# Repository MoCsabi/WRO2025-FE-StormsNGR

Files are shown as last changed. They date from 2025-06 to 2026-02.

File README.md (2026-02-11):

# Introduction
We are the StormsNGR team from Hungary, and we competed in the 2025 WRO Future Engineers category. This was our second year competing after a very successful first year, for which you can find our documentation [here](https://github.com/MoCsabi/WRO2024-FE-StormsNGR). We will be keeping that repository as it is, and will be updating this repository for the 2025 season.

# Results
We once again managed to earn a spot on the podium with 3rd place, a result we are very proud of 😊. We will be keeping this repository as is to help those who are interested study our complete 2025 season solution. For the 2026 season you can follow our progress in the [WRO2026-FE-StormsNGR](https://github.com/MoCsabi/WRO2026-FE-StormsNGR) repository.

## The team
>Team members
- **Csaba Molnár** from [Budapest University of Technology and Economics](https://www.bme.hu/en) Faculty of Electrical Engineering and Informatics
  - csabi@molnarnet.hu
- **András Gräff** from [Budapest University of Technology and Economics](https://www.bme.hu/en) Faculty of Mechanical Engineering
  - andrasgraff@gmail.com
- **Levente Molnár** from [Sóskút Károly Andreetti elementary school](https://iskola.soskut.hu/)
  - levente@molnarnet.hu
>Coach
- József Balázs Gräff
  - graffjozsefb@gmail.com

Links to our socials:

- **Facebook**: https://www.facebook.com/stormsteam/
  - Here you can find updates about the team
- **YouTube**: https://www.youtube.com/channel/UCyzm_Su7qoRCof-ZpbG_9Ig
  - Here you can watch videos about past competitions
- **Instagram**: https://www.instagram.com/storms_team_hun/
  - Cool posts and updates about our, and our sister-team StormsRMS' preparation for upcoming competitions

# Abstract
Our solution is an autonomous car powered by a Raspberry Pi coded in Python, responsible for the main challenge logic, and an ESP microcontroller coded in C, responsible for controlling the motors and processing sensor data. The two devices communicate using UART. We use a 360° 2D LiDAR combined with a gyro to always know where the robot is on the mat. Detection of the traffic sign's color is done by combining the output of the LiDAR with the camera feed to know exactly where the object is. We use ackermann steering geometry calibrated so the car can leave the parking space in one continuous arc. Driving is powered by 1 DC motor through a differential gearbox designed from scratch, with a top speed of around 2.6 m/s.

# Table of contents

### [Our journey](/Our%20Journey.md)
### [Ideas and principles](/Ideas_and_principles.md)
### [Hardware documentation](/schemes/README.md)
### [Software documentation](/src/README.md)
### [measurement- The robot's mechanical characteristics](/The%20robot's%20mechanical%20characteristics.md)
### [RpiCode development tool documentation](/other/README.md)
### [Videos](/video/video.md)
### [Team Photos](/t-photos/)
### [Vehicle Photos](/v-photos/)

# Special thanks
Special thanks to Zsolt Molnár for all the mentoring he's done for us, József Molnár from the [Budapest University of Technology and Economics](https://www.bme.hu/) Faculty of Mechanical Engineering for helping us with the preparations, György Fenyvesi for helping us develop our prototype [custom made interconnect panel](/schemes/README.md/#custom-made-interconnect-panel-wiring-with-connections-labeled), and a bunch of others for helping us by reviewing all the documentation. And of course, to both our families for tolerating us taking up the entire living room with the robot mat 🙂.

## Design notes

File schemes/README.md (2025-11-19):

# Hardware documentation and setup guide
The robot is made up of a lot of different sensors, motors and two processing units, the ESP microcontroller and a Raspberry Pi. The car uses ackermann steering geometry and one DC motor through a motor controller with a differential gearbox we designed and printed from scratch. We had to create a lot of custom 3D printed components and even a custom interconnect panel to help with complicated wiring. The power to the robot is supplied by a 11.1V lithium battery and is later converted to 5V by a step-down module.

## List of components
We installed a lot of sensors and other components on the car, here is a list of each of them with a link and some additional notes:
- **Ackermann steering mechanism** and **base plates** [Ackermann Intelligent Car](https://www.hiwonder.com/collections/robotic-car/products/ackermann-steering-chassis?variant=40382428381271)
  - originally 270 x 197 mm, 960 g
- **Steering servo** [Carson CS-3](https://www.amazon.co.uk/Carson-500502015-500502015-CS-3-Servo-3Kg-JR/dp/B0037Y93CW)
  - Operating voltage 4.8 - 6 V, torque 31 Ncm, operating time 0.17 sec/60° dimensions : 38.5 x 19 x 32 mm, weight: 39 g
- **DC motor** [Hiwonder JGB37-520R30-12](https://www.hiwonder.com/products/hall-encoder-dc-geared-motor)
  -  Operating voltage 12V, torque 15 kg*cm max 3.2A, 280 RPM, 440 pulse-per-revolution encoder
- **Single Board Computer** [Raspberry Pi 5 4GB](https://www.raspberrypi.com/products/raspberry-pi-5/?variant=raspberry-pi-5-4gb)
  - Operating voltage 5V/5A USB-C, 4 USB ports, 40 pins
- **Microcontroller (ESP)** [NodeMCU-32S](https://www.hestore.hu/prod_10037961.html)
  - Operating voltage 5V, 2*19 pins, dimensions: 49.5 x 26 mm
- **Custom interconnect board**
  - ESP pins insert into this, PCB that groups common pins near each other, helps with wiring
- Inertial Measurement Unit (**IMU**/**Gyro**) [BNO085](https://www.hestore.hu/prod_10044901.html)
  - Operating voltage 3.3V, drift 0.5°/min, dynamic rotation error 4.5°
- **Motor driver** [DRV8871-MK](https://www.hestore.hu/prod_10048030.html)
  - Output 3.6 A max
- **Step-down module** [XL4015-3D-STDN-PSU](https://www.hestore.hu/prod_10042112.html)
  - Output 5V/5A, displays voltage, useful for checking battery state
- **Battery**
  - Bundled with Ackermann Intelligent Car, 11.1V, 6000mAh, lithium
- **Display and buttons panel** [Led&Key](https://www.hestore.hu/prod_10042203.html)
  - 8 seven segment displays, buttons, LEDs
- **Active buzzer** [Z2 buzzer (KPI-G2330E)](https://www.hestore.hu/prod_10029469.html)
  - Operating voltage 3-24V DC, 3700 Hz, 83 dB, dimensions ⌀23x10mm
- **Power switch** [ST 1/BK (MRS-1)](https://www.hestore.hu/prod_10023322.html)
  - Dimensions 19.3x12.9mm
- **LiDAR sensor** [STL-19P, D500 development kit](https://www.waveshare.com/wiki/D500_LiDAR_Kit)
  - Dimensions 38.6 x 38.6 x 34.8 mm, range 0.02-12 m, frequency 5-15 Hz, accuracy ±45 mm
- **Camera** [Raspberry Pi Camera Module 3](https://www.raspberrypi.com/products/camera-module-3/)
  - FPC connector, standard lens, RAW10 color format, vertical FOV up to 41°, horizontal up to 66°
- **Ball bearings**
  - 3 pieces of 7(inner diameter)x19x6 mm and 1 piece of 6(inner diameter)x12x4 mm
- **USB-TTL bridge** [CH341T-V3-M](https://www.hestore.hu/prod_10044421.html)
  - supports both 3.3V and 5V, enables us to use another serial port on the Pi for UART communication
- [**Carbon fiber Lego technic axle**](https://joooooy.com/products/moc-carbon-fiber-technic-axle-4519-3705-32073-3706)
  - can be cut to size, heavy-duty, won't bend as easily
## Assembly - Overview

This section serves as an overview of the design philosophy of the robot. For more details about the actual driving and steering mechanism see [Drive](#drive), and for building instructions see [Building instructions](#building-instructions).

Our robot utilizes ackermann steering geometry and differential drive. We have 3 decks, a bottom deck (or lower deck) for the servo, driving mechanism and the power supply. On the middle deck we have the Raspberry Pi, the main control unit coded in python, responsible for the main challenge logic, and the ESP microcontroller, the secondary control unit coded in C, responsible for receiving sensor data and controlling the motors. The LiDAR sensor is is also mounted here. The third deck is about half the size of the other decks, it houses things like the motor driver, the IMU, the display panel and the step-down PSU.
image showcasing the 3 decks on the robot image of the car with connections between components
(Sketch that illustrates the connections between the different components of the robot)

For steering we used a solution that can be found in many RC cars, we took one from the Ackermann Intelligent Car by HiWonder. After calibrating the geometry to the length of our car we maximalized the steering range to ensure tight turns. We also replaced the steering servo for one with less power consumption and slightly smaller size. For the driving motor we used a 1:10 ratio 12V DC motor and secured it with 90° mounting brackets. The D-shaft of the motor goes inside the custom-designed differential gearbox, where we convert to a lego technic X axle, on which the wheels are mounted. For the rear wheels we used thin Lego wheels, and for the front wheels thin Lego compatible custom 3D printed wheels to make the robot less wide, and make parking easier. Due to the many heavy installments, such as the motor and the power supply, the center of gravity is low, which is ideal for track stability and turning.<br> On the middle deck we have the Raspberry Pi and the ESP-32 microcontroller with its pins mounted on a custom interconnect PCB. It helps with the wiring by routing certain pins next to each other and allowing us to use ribbon cables, making everything much cleaner. This deck is separated from heavy-duty equipment like the motor which cause electrical noise that could interfere with the controllers. The LiDAR sensor is also mounted here with a special mounting bracket, ensuring the widest FOV possible. The base of the camera tower is also mounted here.<br>The third deck is much smaller, the main reason we installed it was the lack of space for the remaining components, while also keeping the car small and light. Importantly the Led&Key input and display panel is also installed here for easy access. The camera tower ensures the camera is looking in front of the robot with a 15° vertical tilt down. The final size of the robot is 26.8 cm long, 15.8 cm wide and 20.9 cm high. It weighs 1246 grams.

## Wiring diagrams
The colored squares represent the cable colors on the robot.
### ESP microcontroller (NodeMCU) pinout with connections labeled:
This illustration is most important for the source code, since everything is actually wired through the custom-made board for the ESP.
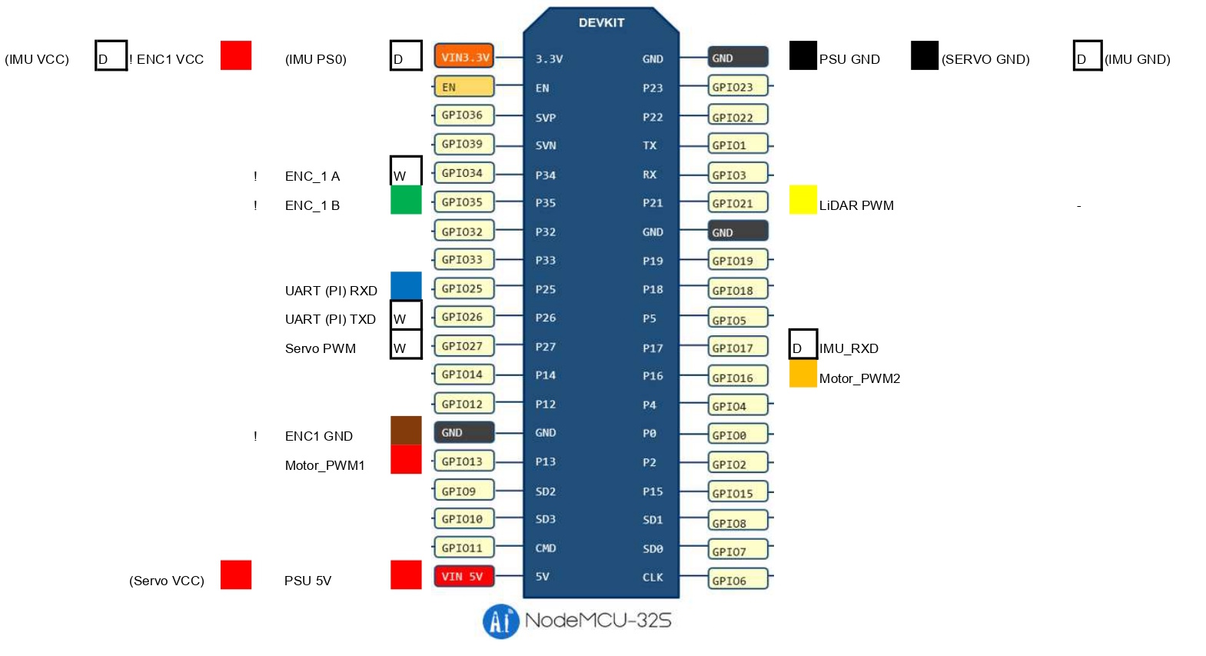
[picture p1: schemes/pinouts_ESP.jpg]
ESP wiring diagram

(ENC-Motor encoder, PI-Raspberry Pi, D: directly connected, !: not wired through the interconnect panel)

### Raspberry Pi pinout with connections labeled:
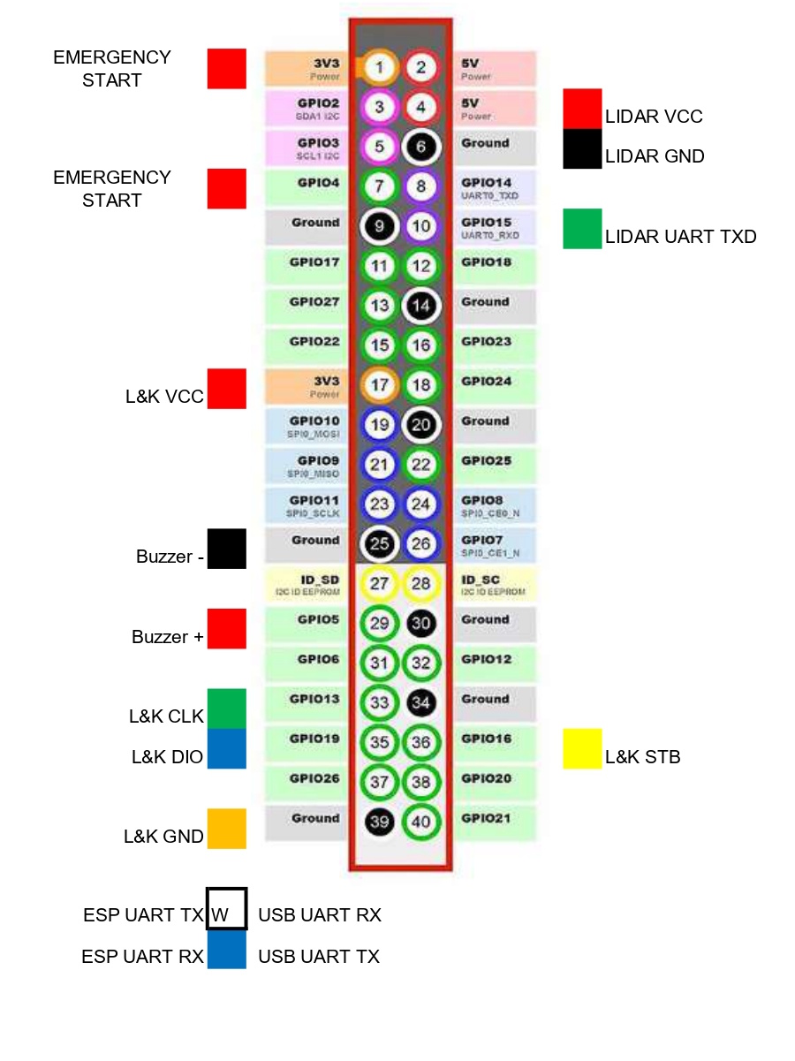
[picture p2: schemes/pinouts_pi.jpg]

(L&K-Led and Key panel)
### Motor controller wiring:
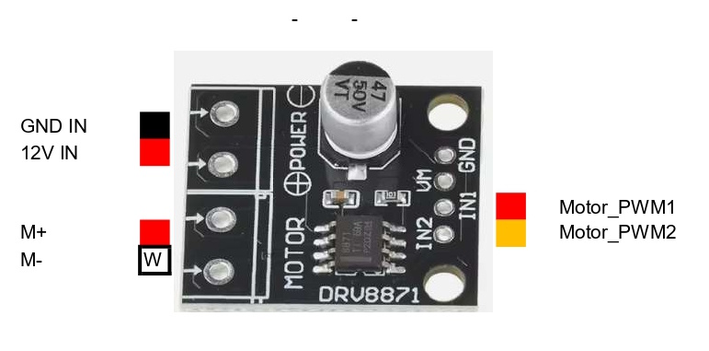
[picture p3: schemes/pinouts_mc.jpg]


All of these can also be found in the form of an excel spreadsheet in the [pinouts.xlsx](pinouts.xlsx) document.

### Custom interconnect PCB schematic and wiring:

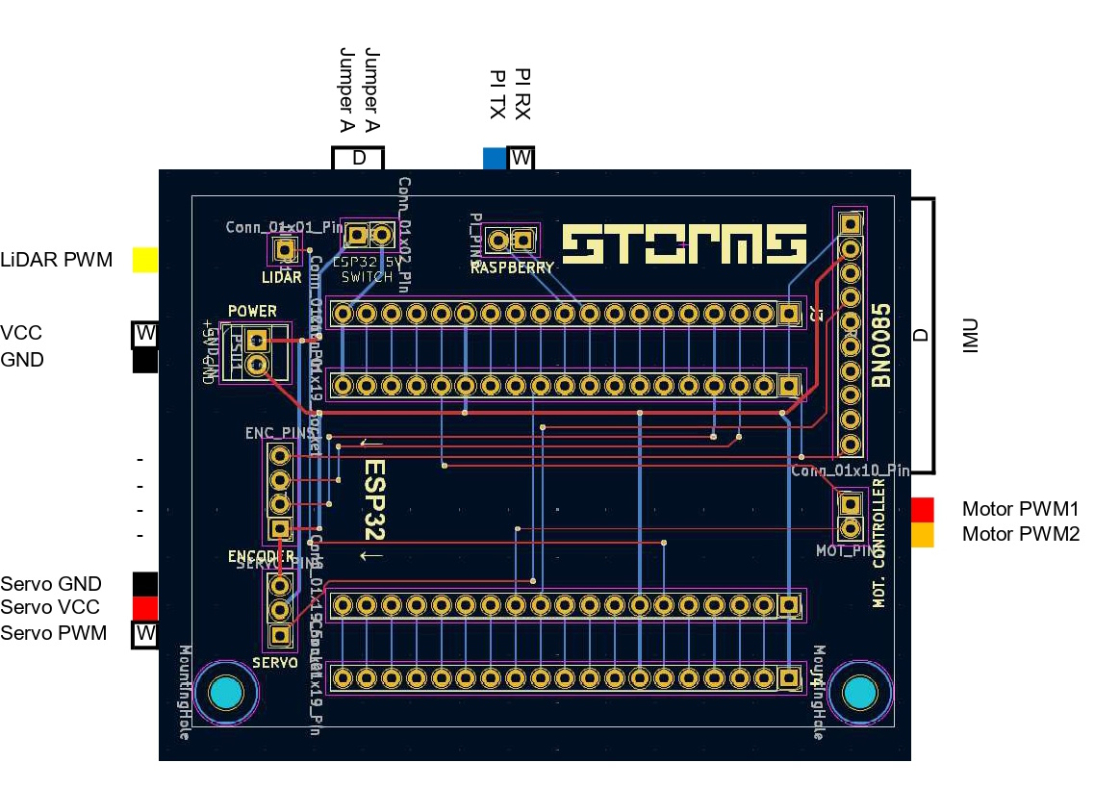
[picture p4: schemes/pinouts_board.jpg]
PCB pinout


*Note: the red wires are on the top, the blue ones are on the bottom of the PCB, which let us connect everything in a clear, simple matrix layout without collisions*

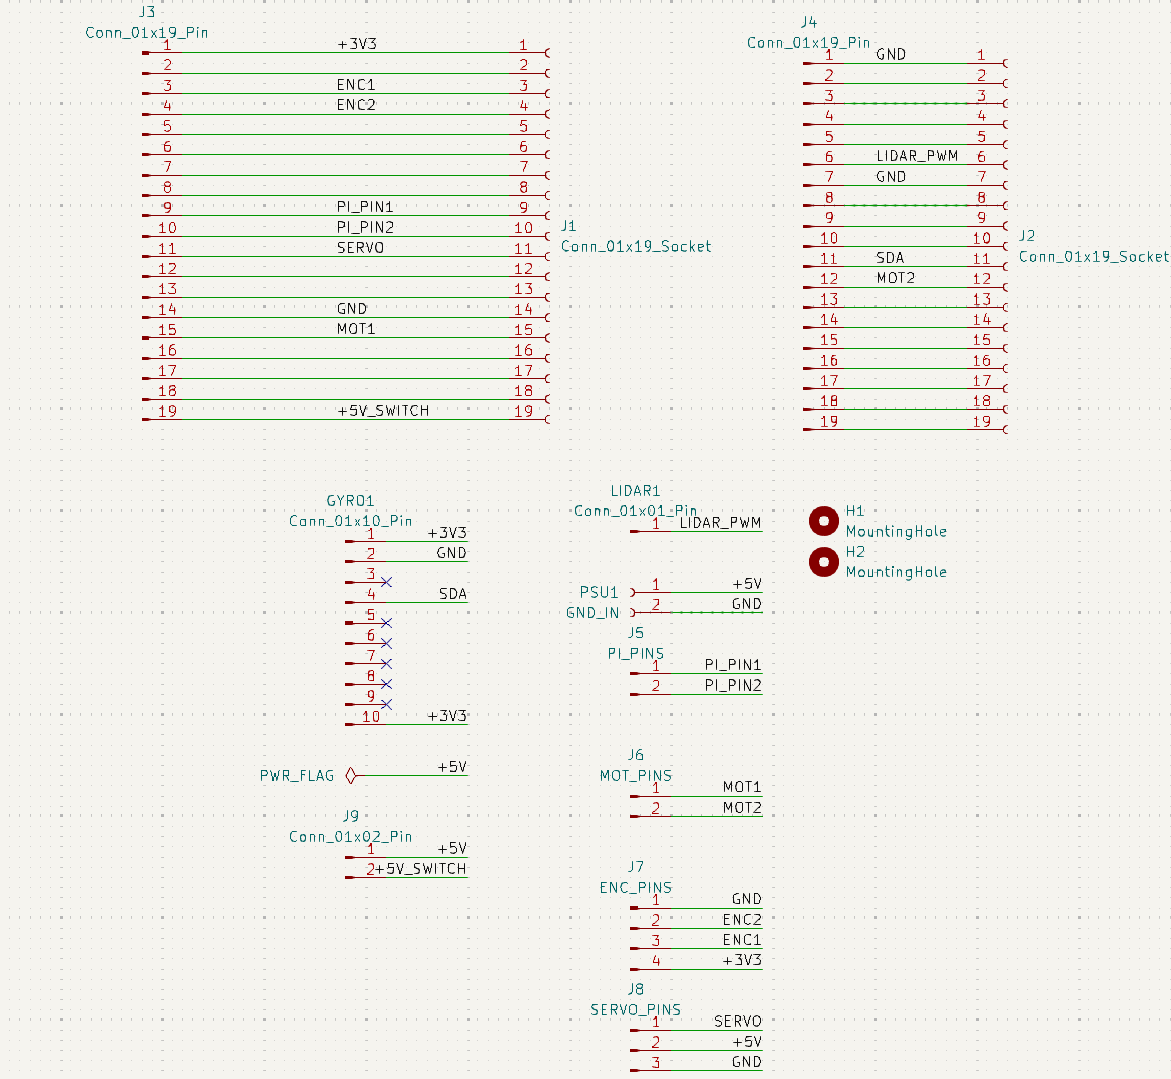
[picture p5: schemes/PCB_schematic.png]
PCB interconnect wiring


Some extra rules had to be employed in order to ensure the PCB working properly. First, the GND and +3V3 as well as +5V wires were thickened, since they deliver much more current than everything else. Another big factor was the 5V wiring itself: the ESP could either get its 5 volt power through the built in pin or USB-C port, but not both without that causing issues (for example, it managed to break the USB port of two of our ESP-s). Because of this, a jumper bridge has been added, if the `ESP32 5V SWITCH` pins are not connected, the ESP must be supplied through the USB port, otherwise power delivery is done through the dedicated pin.

The PCB project, along with its BOM can be found in the [schemes/wro_nyak](/schemes/wro-nyak/) subfolder.

## Power
The robot's power supply is provided by a central accumulator (battery).
We considered powering the motors and the control system from separate power sources due to their differing requirements and to limit the electrical interference (noise), but ultimately decided on a common power source for simplicity. The 11.1 V, 6000 mAh lithium accumulator provides more than sufficient capacity for us. A lower capacity device would have also sufficed and while being lighter, but the ability to avoid constant recharging is a great advantage for us during the testing periods. For safety, the accumulator is easily removable via a detachable cable. We have a spare unit, enabling us to charge one while using the other. The accumulator connects directly to the main switch via the detachable cable.
The battery's largest consumer is the drive motor. The DC motor connects to the motor driver without voltage conversion. The driver's maximum current is 3.6A, which is sufficient for the motor's maximum current draw of 3.2A. The motor driver includes essential integrated protections (Overcurrent Protection - OCP, Thermal Shutdown - TSD).
The remaining components of the system operate at 5V, which we provide using a step-down power supply. A very useful feature of this power supply is that it displays the input voltage, allowing us to monitor the battery's state of charge. Among the 5V components, the Servo and the Raspberry Pi require significant current, which is handled by the power supply's 5A maximum current output.
A few of the robot's components, mainly sensors, operate at a 3.3V voltage level, but their power supply is provided by the controller (ESP/Pi) they are connected to.

A simple explanation of the power supply hierarchy of our robot.
- Battery `12V`
  - Step-down module `12V-->5V`
    - Steering servo `5V`
    - Raspberry Pi 5 `5V` (from USB-C, can supply `3.3V`)
      - LiDAR `5V`, **180mA**
      - Camera `5V` **200mA** (FFC)
      - Led&Key Panel `3.3V`
    - NodeMCU-32S `5V` (from **Vin** pin, can supply `3.3V`)
      - Inertial Measurement Unit `3.3V`
      - Motor encoder `3.3V`
  - Motor driver `12V`
    - DC motor `12V` **~1A**, max 3.2A

## Connections
The different connections used between the components of the robot and their hierarchy:
- Computer
  - Raspberry Pi `SSH`
    - ESP `UART` Pi: **USB-TTL** - ESP: **RXD-GPIO-25, TXD-GPIO-26**
      - IMU `UART-RVC` **(SDA-GPIO 17)**
      - Motor encoder `Digital` **(A-GPIO 34, B-GPIO 35)**
      - Motor driver 2x`PWM` **(PWM_1-GPIO 13, PWM_2-GPIO 16)**
      - Servo `PWM` **(Signal-GPIO 27)**
    - LiDAR `UART` **(TX-GPIO 15)** 
    - Led&Key panel `Data, Strobe, Clock` **(DIO-GPIO 19, STB-GPIO 16, CLK-GPIO 13)**
    - Buzzer `Digital` **(+-GPIO 5)**
    - Camera `FFC`

The actual communication between the components is detailed in the [software documentation](/src/README.md#sensors-and-motors).
## Drive
For steering, we utilize Ackerman steering geometry.
In short, the inner wheel turn slightly more than the other, so the robot stays on the same arc without any slippage. Here's an image from the [Hiwonder documentation](https://drive.google.com/drive/folders/11k0gbcZExI4076KJ1d_CCIdDlopuYUwO) that illustrates the principle:

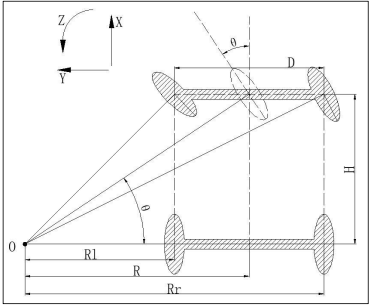
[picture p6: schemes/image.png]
ackerman geometry


The steering mechanism has to be assembled so the steering pivots are on the line between the steering kingpin and the center of the rear axle.

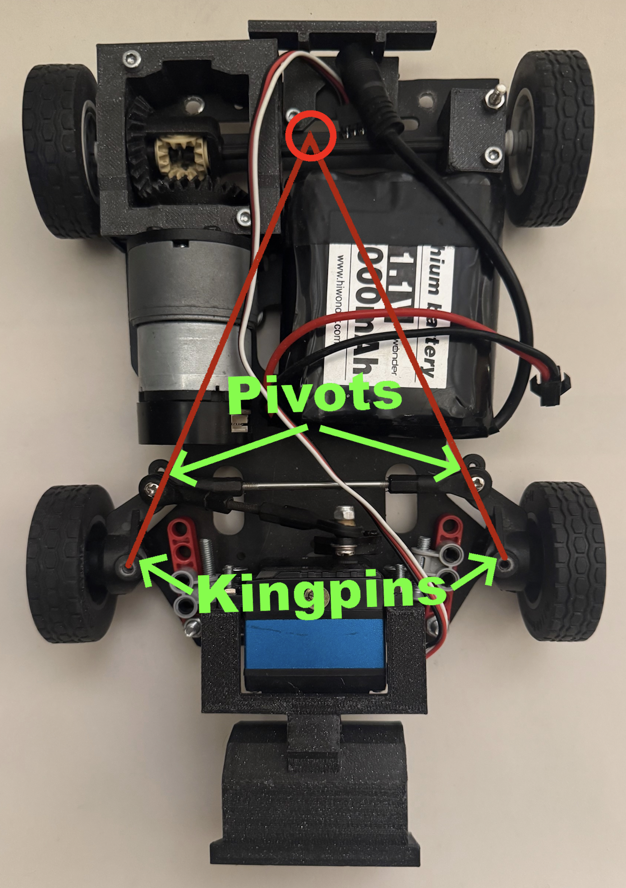
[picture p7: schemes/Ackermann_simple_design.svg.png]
ackermann geometry illustrated


We use two kinds of turning, turning along an arc or turning until a target degree is reached using **PID** control with the gyro. For turning along an arc we can use this formula to calculate the correct servo angle for an arc given $R$ radius:
$$θ=arctan \left( {H \over R} \right)$$
($H$-distance between front and rear axles, $R$-target radius)

For driving we wanted to use [Electronic Differential](https://en.wikipedia.org/wiki/Electronic_differential), which is simply simulating a differential using software by calculating the required force using the current angle of the servo.
The formula for calculating the correct speeds of the two motors:
$${V_l}=\frac V R*\left( R-\frac D 2 \right)$$
$${V_r}=\frac V R*\left( R+\frac D 2 \right)$$

($V_l$- left motor speed, $V_r$- right motor speed, $R$- current arc, $V$- robot tangential speed)

This would have been the most ideal solution, as this way we could avoid complicated hardware components and also use the power of 2 DC motors easily. This is also how many modern real life electric cars operate (such as the [Tesla Model S](https://en.wikipedia.org/wiki/Tesla_Model_S#Powertrain) for example), and since the competition's main goal with car restrictions seem to be realism we hoped this solution would be accepted. However, with the reasoning that cheating by not accurately simulating a differential would be hard to detect, this solution was not allowed by the head judges. This way we had to design and 3D print a differential gearbox from scratch, and only use 1 DC motor. 

First, we created a mechatronic model of the drivetrain starting from the motor to the wheels.
The so-called mechanical impedances of the components ($Z_{force} = \frac{1}{m\cdot s}, Z_{torque}=\frac{1}{J\cdot s}$ in the Laplace domain)

Impedance network of the car's drivetrain

From this, using a Jupyter notebook, all the parameters of the system could be calculated.
The moments of inertia were generated using the `numpy-stl` library, the rest were of the values were measured manually. From this we concluded that with the current setup the transmission ratio should be changed as much as possible to favor lower torques and higher rpm. We designed two helix gears with 1:1 transmission with Lego technic axle slots for heavy duty carbon fiber axles, which gave us more than enough maximum speed at 2.6 m/s. We made sure to use ball bearings where the axles are supposed to rotate freely. The design process is further detailed in [The design process of 3D printed parts](#the-design-process-of-3d-printed-parts). A simple diagram showing this solution:

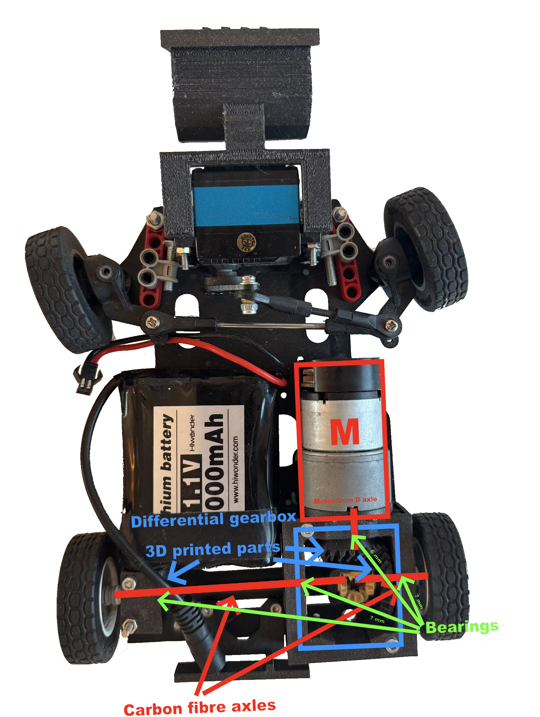
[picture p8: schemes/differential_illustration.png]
diagram


($M$- DC Motor)

# The design process of 3D printed parts

Designing and printing out different parts of the robot was one of our biggest task where we had to take a lot of things into account in order **for everything to work properly**. Sometimes we had to rely on **trial and error** to make sure everything was how we wanted it to be.

---

## The steps of The design process:

### 1. Coming up with the general shape and location of the part
  
  In This part we first had to take a close look at how our robot looked so far then try to figure out **how and where our soon to be designed part could fit.**
  Things we had to look out for:
  - Having an appropriate amount of space for the parts.
  - Having the right screw holes to be able to make a good mounting mechanism.
  - Making sure that putting the part there wouldn't interfere with anything else.
  
  After we found to correct location we made a very, **very simplistic sketch** of what we wanted.

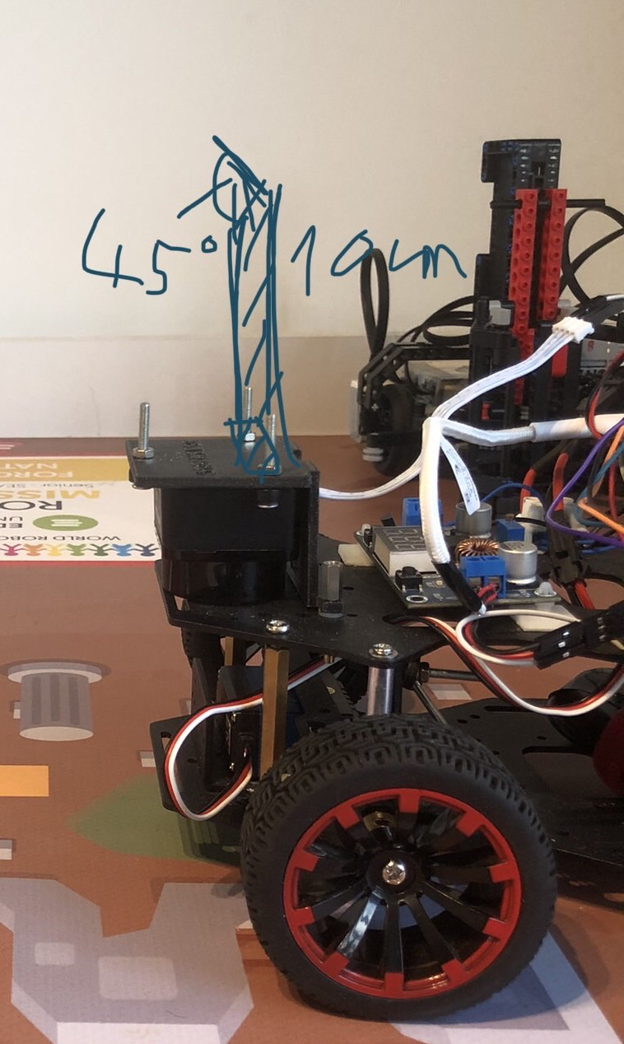
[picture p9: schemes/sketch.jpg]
Sketch for the camera stand
  

### 2. Gathering usable documentation
  This is maybe the most important part in the process, because the quality of the documentation available **can make or break a design**. While taking your own measurements is viable, it is a lot simpler to use a documentation and yields **more precise results**.

### 3. Making the model
  We used *Autodesk Fusion 360* for designing our parts, however any industrial software like *Autodesk Inventor* can be used as well. In the modelling process there are a couple of things to remember:
  
  - Make sure that any measurement given in a documentation seems realistic, **since we have seen mistakes even in official documentations**.
  - Always double check any calculation and check the dimensions relative to multiple sides, because **it may look alright from one side, but may be completely unusable from another**.
  - Use your software's built in physics simulators to check for weak points and **always make sure it can handle the stress it may be placed under**.
  - When done export the file as an **.stl** so that a slicer can use it.

  Don't worry if you don't know how to make 3D models yet, it is a lot easier than people might think. The process in simple terms just requires you to make a sketch/blueprint like below and extrude it out into 3D space.
  
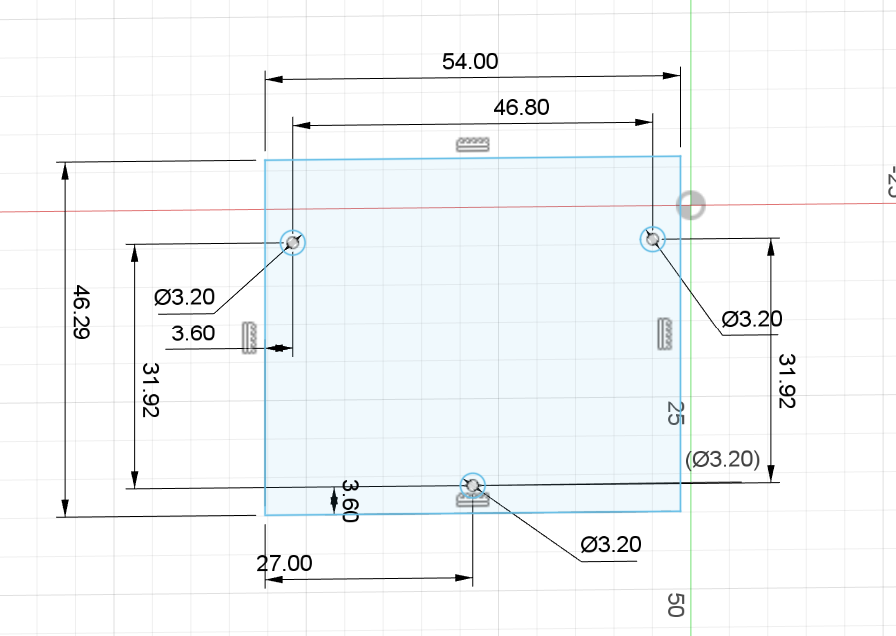
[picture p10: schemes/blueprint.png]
Example of a sketch in Fusion 360
  
  
### 4. Exporting the G-code
  We printed our parts with a *PRUSA mini+* and used *PrusaSlicer*, but any 3D printer and software will do as long as it has a **large enough print area** and supports the **right types of filament** (we use PLA but PETG should also work). We suggest that for more **aesthetic parts a 30% infill** is used and for **more structural ones a 60%**. It may also seem trivial but the **angle and orientation** in which the part is printed matters a lot to. For example **for tires a $45°$ tilt** is suggested to make sure that it **won't come apart parallel to the print lines.**

### 5. Printing out the part
  Here there is not much to look out for, just make sure that the **printer's settings are right,** there is enough filament and the **supports are sufficient.**

---

## How we applied these steps and the difficulties we faced

### The lidar mount

  The lidar mount was the *first part* which we designed ourselves and the part that makes it so that the lidar can see **exactly what we want it to see.** While the robot chassis had the right screw holes to mount it to begin with, the problem we faced relied on the angle in which the lidar shoots out its beams of light. It was slightly angled to shoot upwards. Because of this the lidar was **seeing above the walls** of the map which was a lot less than optimal. Our solution was to flip the lidar upside down to **lower the starting point of the beams and make them shoot slightly downwards instead.**
  The main things we had to look out for in this part were:
  
  > **Making sure that it won't start tilting in random directions throughout the round.**
  
  The way we solved this was, that the mount just makes it so that it doesn't move horizontally, but vertically it doesn't give much support, **letting it lie directly flat on the vehicle**.

  > **Mounting it securely while leaving enough space for a wide field of view.**

  We solved this by only mounting it from the back with two screws, which does give up a lot of stability, but we **still found it sufficient for this use case**.

  > **Making the range of the Lidar as wide as possible while also allowing it to see backwards**

  This was the easiest since we just had to have an empty slot in the back of the mount.

  [The documentation we used (Page 7 is the most important)](https://www.ldrobot.com/images/2023/05/23/LDROBOT_LD19_Datasheet_EN_v2.6_Q1JXIRVq.pdf)

  This part worked flawlessly so we have been using it ever since last year's competition.

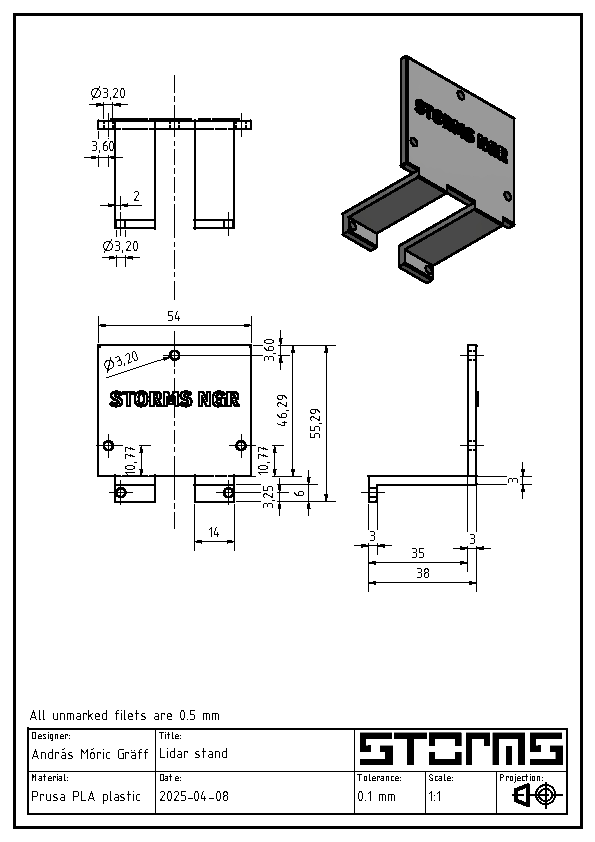
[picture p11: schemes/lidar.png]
Lidar mount
  

### The camera stand
  
  The camera stand was one of the parts that needed an almost complete redesign over last year, but this time it did not require four iterations to get the final result.
  The mounting area stayed the same, using two screws for security and having the main body elevated in order to **allow the Lidar's laser to pass through below it.**
  The top part however required a complete redesign since we changed cameras. It needed to keep the camera at a **height of 20 cm with a depression angle of 15°** to get the correct image. This made the piece quite tall, so a few security bars were added for support. To mount the camera we made small pins that fit exactly into the screw holes of the camera. To make it so that it doesn't fall out, a lid can be slotted in from the top. Between the lid and the camera we also inserted a few pieces of paper to cushion it and make sure nothing gets damaged.

  [The blueprint we used](https://datasheets.raspberrypi.com/camera/camera-module-3-wide-mechanical-drawing.pdf)
  [Link to previous year's version](https://github.com/MoCsabi/WRO2024-FE-StormsNGR/blob/main/schemes/README.md#the-camera-stand)

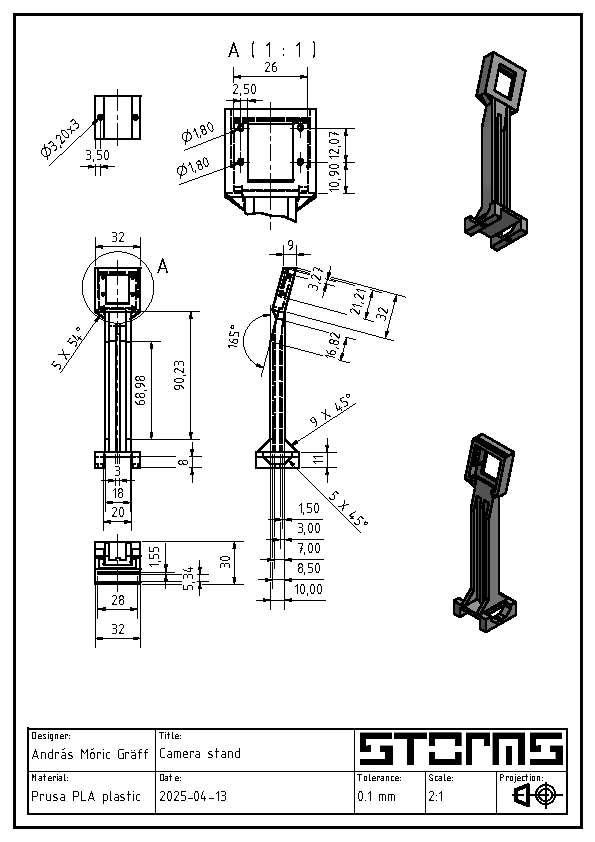
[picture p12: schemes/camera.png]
camera stand
  

  The lid is as simple as this, so it doesn't even need to be 3D printed, a piece of cardboard would work just as fine.
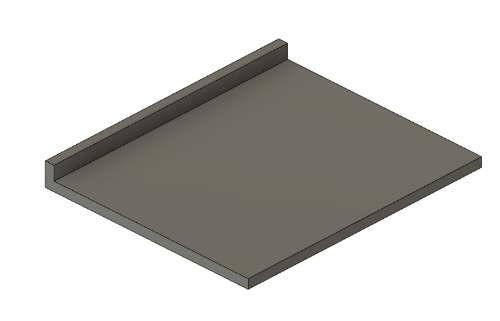
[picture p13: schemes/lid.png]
The lid
  

### The tunnel
  We adjusted the lidar mount and camera stand to enable the **lidar to see backwards,** however another part was needed to be designed to make sure that **nothing obstructed the view.** This was the most simple model we ever made, since it really is just a **little tunnel** meant to clear the way.
  
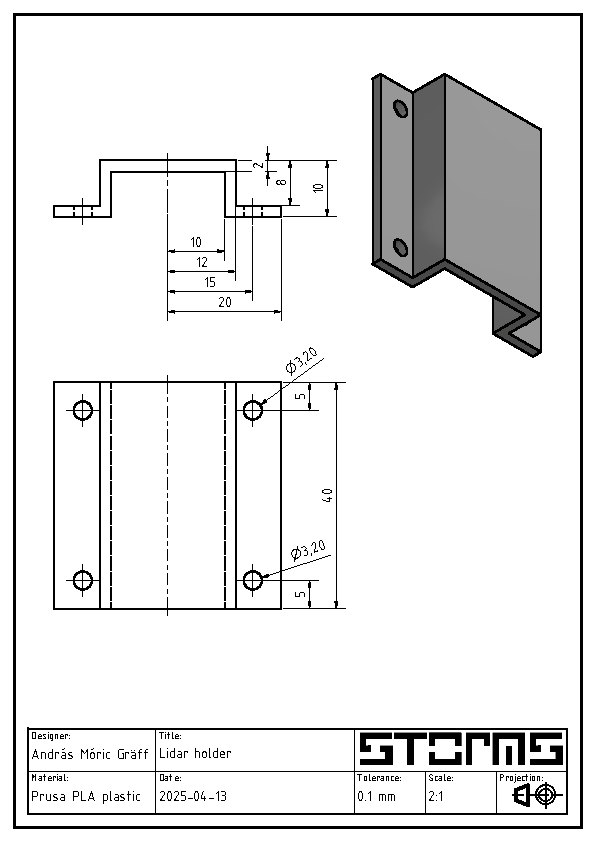
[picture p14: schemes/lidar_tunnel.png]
lidar tunnel
  
  
  It is mounted using four screw, which is a bit of an **overkill,** since realistically it won't really be put under any stress. Because of this we only ended up putting screws into the two rear holes.

### The differential gear
  This year we decided to make a custom differential and replace the old Lego one. This model required by far the most engineering knowledge.
  The differential was designed with a few important factors considered:
  >-  **To have a size similar to the previous so it would be easier to implement into the assembly.**
  >-  **To have enough tolerances for 3D printing, but at the same time to minimize the backlash between the various gears and - of course - to achieve maximum efficiency.**

  In order to achieve this, we decided to use two helical gears, with one replacing the gear part of the old differential, while not changing the rest. The helical gears allow for better contact between the gears, and therefore a **higher efficiency when the car goes forwards.** Size wise both gears are the same size now (due to the 1:1 gear ratio), their diameters are about equal to the bigger gear in the old differential, so the main axle could stay almost identical to before, with only the motor's position changing slightly.

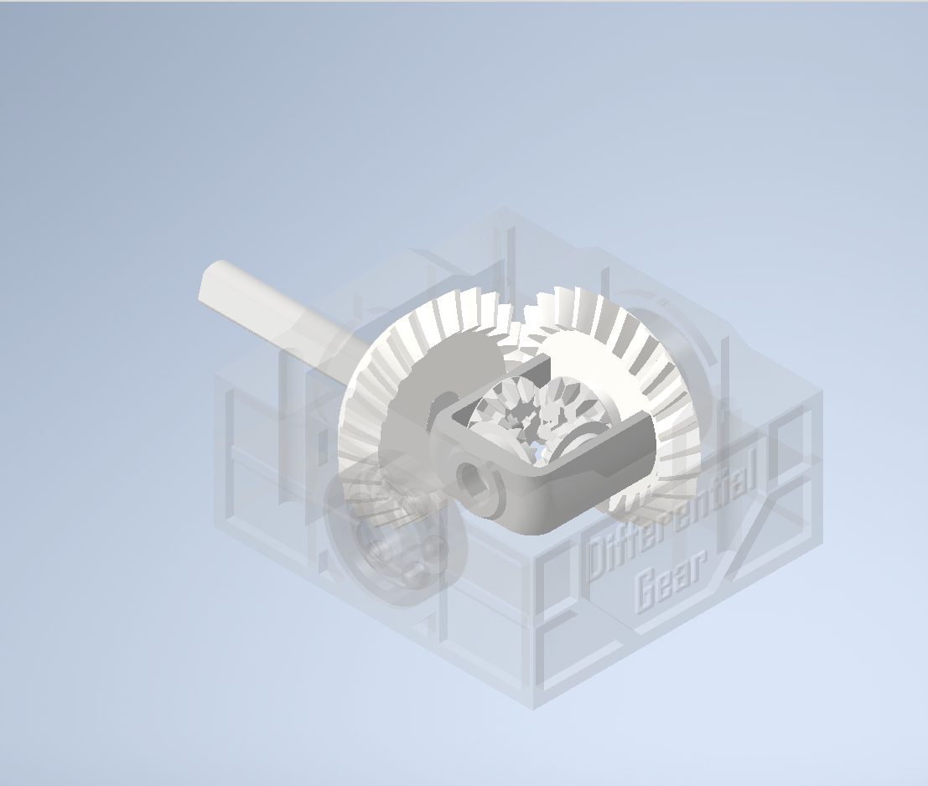
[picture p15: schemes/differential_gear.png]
differential gear
  

### The differential gear frame
  With a new differential we also required a new frame for said differential. The frame is what holds differential in the air so that it doesn't touch anything, and **has embedded bearings to reduce the friction** between the frame and the axles. We used bearings last year as well but this year we made a few improvements in that area.

  >- **Made the slots larger that can accompany larger bearings that provide more support and enables the usage of fitting rings on the axles.**
  >- **Split the model into two and added walls for the slots to make the bearings and the fitting rings unable to move.**

  These changes made the frame a lot more secure, since we had problems with the bearings and axles shifting previously.

  [Link to previous year's version](https://github.com/MoCsabi/WRO2024-FE-StormsNGR/blob/main/schemes/README.md#the-differential-gear-frame)

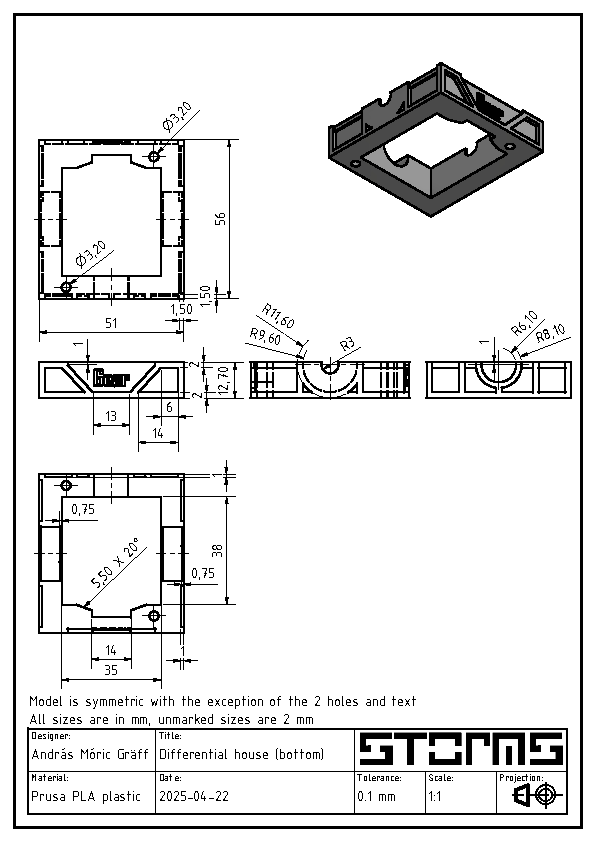
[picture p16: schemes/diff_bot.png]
bottom of the differential
  
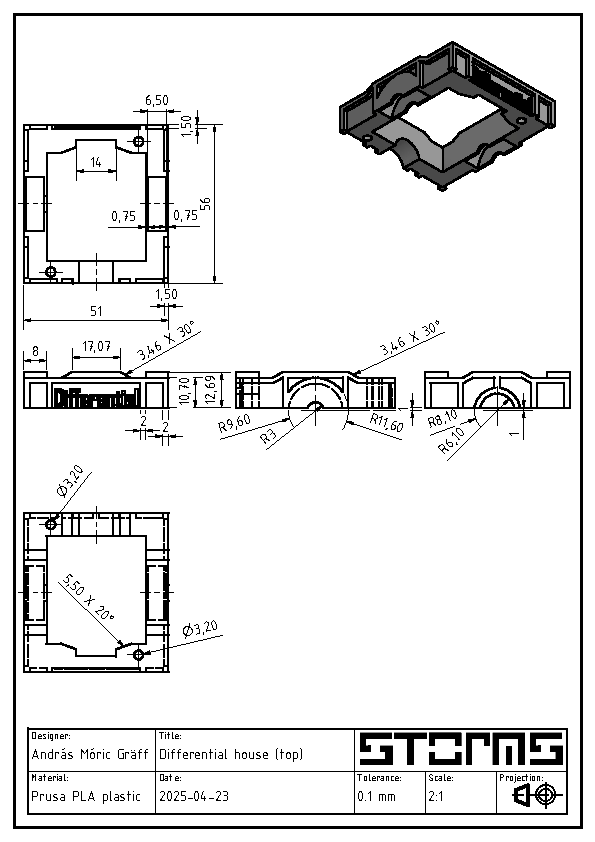
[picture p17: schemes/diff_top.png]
top of the differential
  

### The assembly of the full differential gear

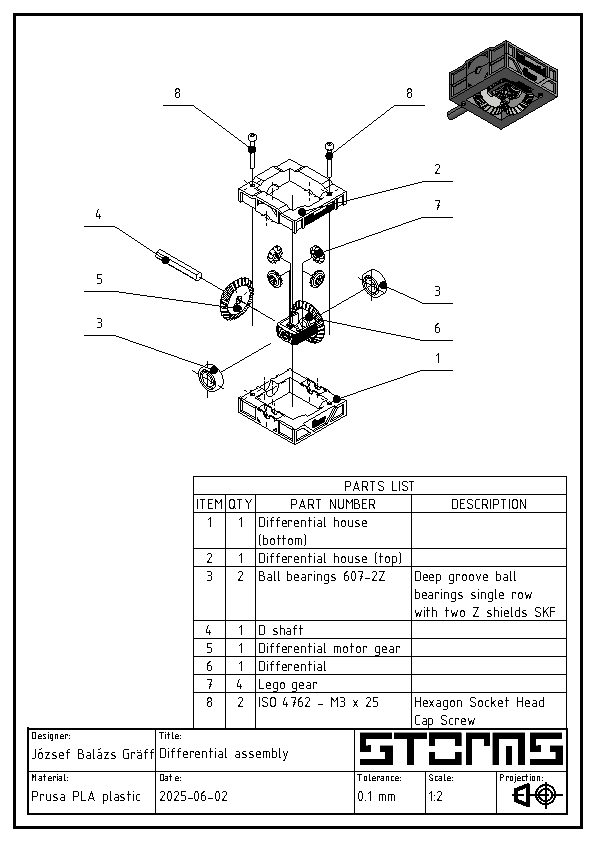
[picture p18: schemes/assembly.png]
differential gear assembly


### Accessories for the differential gear

  The differential gear and house works as is just fine, but for our use case we needed a few extras for it.

#### The fitting rings

  As mentioned above, the axles we used required fitting rings in order to fit cleanly into the bearings. The rings then were glued onto the axles, since the frame restricts the movement of the ring, this makes it that the **entire axle can only be moved if the frame itself is disassembled.**

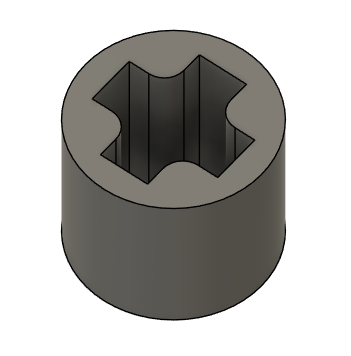
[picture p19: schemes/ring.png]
fitting ring
  

#### The axle holder

  In our robot the differential was on the right side, one of the axles needed to be exceptionally long which would enlarge any potential bending. To counter this we made a securing device which is basically just a box with a bearing in it. Just like the frame, **this was also split in two,** but since this part is completely symmetrical, it only requires one model.

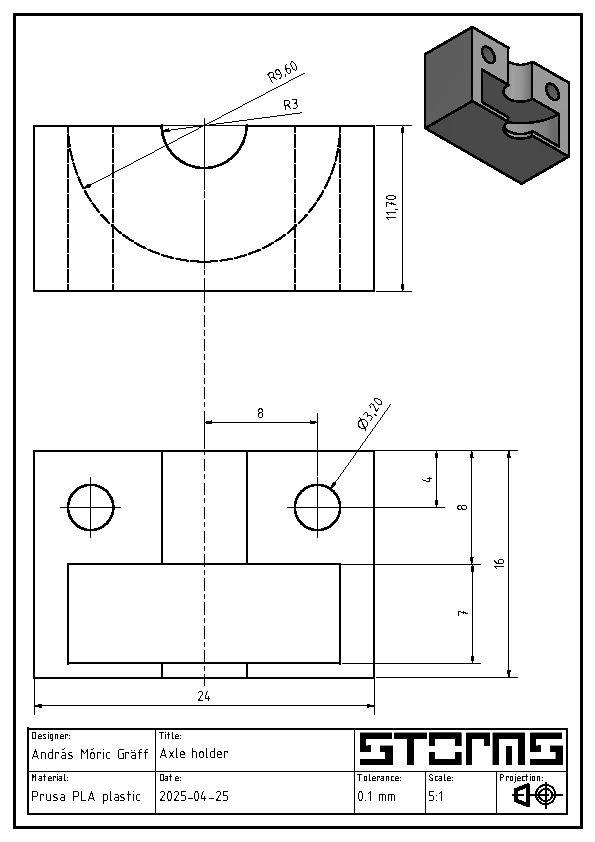
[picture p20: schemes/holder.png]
axle holder
  

### The new wheel

As mentioned before, to save parking space, we decided to switch to thinner wheels, but that caused problems on the front, when mounting. To fix this, we found an STL file of the rims we used online and modified it. We only made two small adjustments.

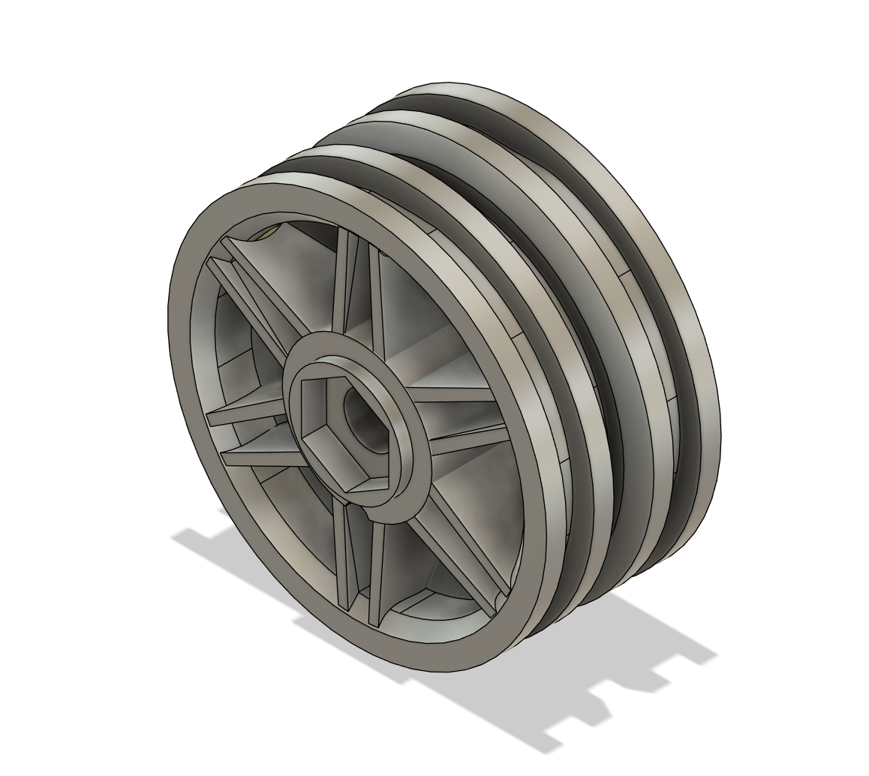
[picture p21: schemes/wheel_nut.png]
new rim


>- **We filled the axle hole in the middle of the wheel and inserted a circular hole that an M4 screw can fit through.**
>- **Addded a hexagonal indent to the outside which can fit an M4 nut.**

Applying these adjustments made the mounting of the front wheels a lot more secure, and also made them take a more straight path on the road, whereas before, there was a slight wobble when going straight.

### Aesthetic pieces

To make our robot fit its name **Dózer** a lot better, we made a few design parts for it as well.

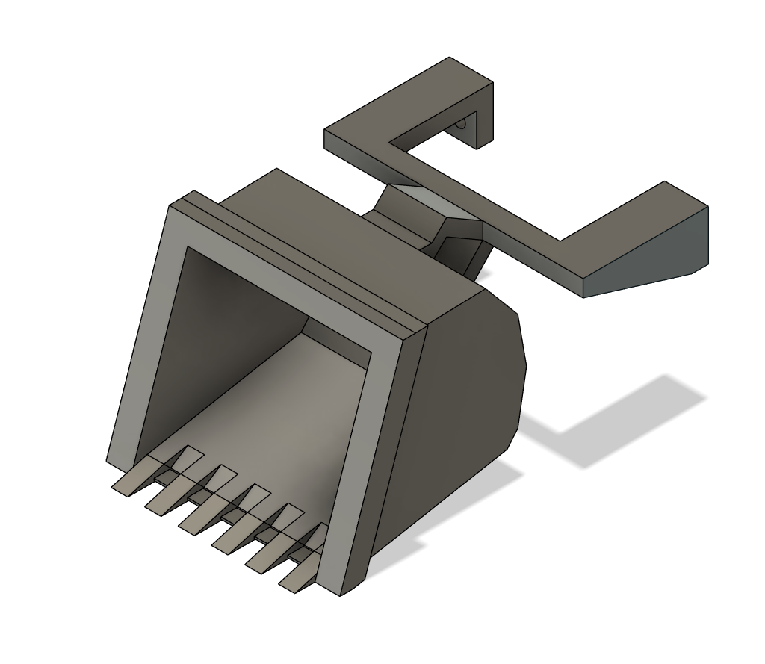
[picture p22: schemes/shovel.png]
Bulldozer shovel
  
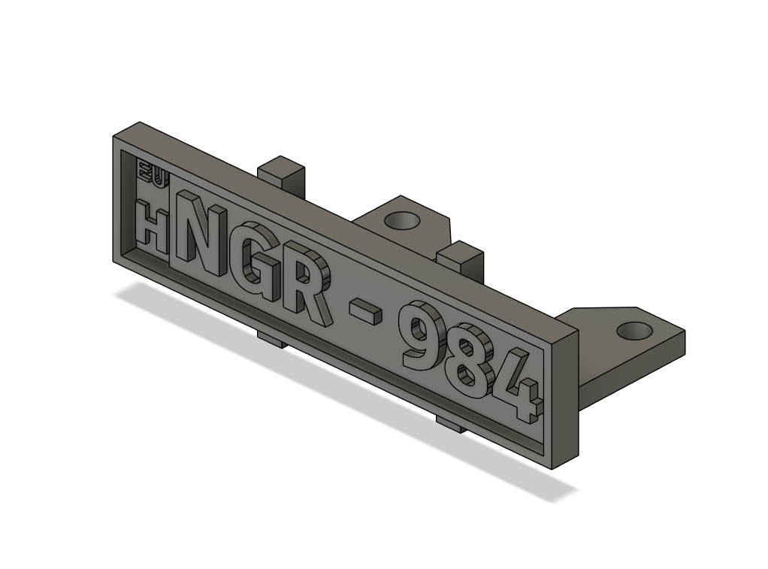
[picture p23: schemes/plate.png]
license plate
  

---

## Conclusion
  
  Designing custom 3D printed parts is hard and while sometimes we can get lucky, like with the lidar mount, **other times it may take a long time and multiple versions until we get it right.** The step by step guide was written according to the **things we learned during our process and things we will be doing in the future.** Making sure that a design is good can be one of the most important steps during the entire process of making a robot. It is of the utmost importance to ensure that **the amazing software one might have doesn't get bottlenecked by bad parts.**

# Building instructions
The 3 decks of our robots are based on the decks from the HiWonder Ackermann Intelligent Car, but you could use any material. Screwholes won't be a problem either, just note the critical measurements and drill them yourself!

First we sawed off parts of the bottom and top decks, as can be seen on this sketch:

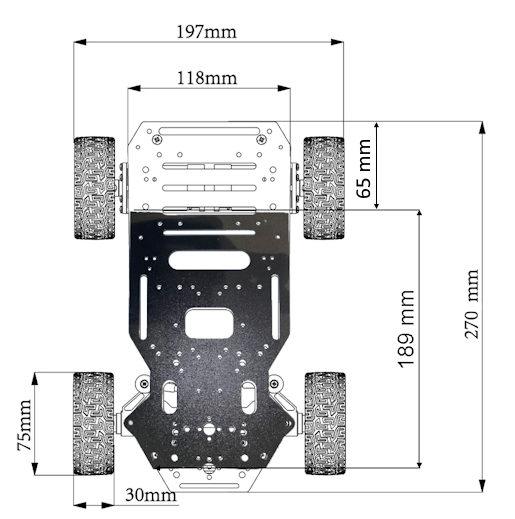
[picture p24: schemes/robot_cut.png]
sketch showing cut bottom deck


Then we repurposed the top deck's rear sawed off part as the third deck.

image showing the third deck

These decks can be mounted on each other with large spacers. The steering mechanism we used from the Ackermann Intelligent Car also plays a role in the structural integrity of the robot.

On the bottom deck we have the aforementioned steering mechanism, differential gearbox, the motor and the battery. How the differential gear-system is made up is detailed in the [Drive](#drive) and [The design process of 3D printed parts](#the-design-process-of-3D-printed-parts) sections. The motor has to be secured down, for this we used the original motor mounting bracket. The battery's position is not important as long as its secured down. This decks intentionally contains most of the heaviest components (the motor and the battery) in order to keep the center of gravity low.

bottom deck of the robot with all components

The middle deck contains the main computing units of the robot, the Raspberry Pi and the ESP microcontroller with the custom-made interconnect panel. It also houses the gyro and the LiDAR sensor, which has to be placed right on the front of the deck, upside down, as secured down with our custom 3D printed LiDAR bracket and ideally supplied with an at least a 230° vision free from any blocking elements. Under the Raspberry Pi is our 3D printed tunnel piece, which has to be installed in a way that both ensures backwards vision to the LiDAR, free from any interfering objects, such as loose cables, and also acts as a support for the Pi and the ESP board. The camera is also installed on this deck by 2 screws, behind the LiDAR. The buzzer can be fixed anywhere, we used a small strip of [3M Double Lock](https://www.3m.com/3M/en_US/dual-lock-reclosable-fasteners-us/) tape, so we can remove it if necessary.
middle deck of the robot with all components

The top deck is installed atop the middle deck by two screws and spacers. It's not suitable to support serious weight, but this is not a problem since the components on there are really light. It houses the motor controller, the step-down-module (PSU) and the Led&Key panel. For the PSU and the Led&Key it was important that they're installed somewhere visible since they have displays with important information, so the top deck was perfect for them. On the Led&Key there are also buttons, which we use to start the rounds, so it's really important that these are supported, since a lot of force is going to be affecting them from above(pressing). We solved this by supporting the buttons from below using spacers. The third deck has to be relatively lightweight to not raise the center of gravity too high.

top deck with all components

All components have to be installed using small spacers to avoid contact with the metal decks. Wiring between components is done using jumper cables, or in some cases thicker power cables for 12V. For more details on the wiring refer to [Wiring diagrams](#wiring-diagrams).
## Conclusion
We had quite a few difficulties during the assembly and planning process, but we are very proud of our work. If there are any problems or further questions don't hesitate to contact us at csabi@molnarnet.hu (Csaba) or andrasgraff@gmail.com (András)

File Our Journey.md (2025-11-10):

# Our Journey

The documentation will begin with the journey we went on this year, our struggles, our biggest achievements and even some funny things we had encountered.

## Our past

WRO has been quite a significant part of our lives for a few years now. While the competition had come with its fair share of hardships it also gave us some of the most important opportunities in our lives. Last year was our first time experiencing tppppphe Future Engineers category and it was a great challenge. We learned a lot and even **managed to secure the title of World Champions,** something we couldn't even dream of achieving before. After such an incredible first experience, we already realized how important this project was for us and eagerly started preparing for this season of WRO.

1st place

---

## The planning phase

In the first phase of development, we mostly did **planning and information gathering.** We already learned last year just how important it is to collect information and have concrete plan. At our first meeting we wrote down what we needed to improve over last year, which areas of our robot required more work.

This was what we came up with:

* Getting new camera with manual image processing
* Making custom made differential gear with higher efficiency, speed and less play in the wheels
* Speeding up our Lidar sensor for a higher refresh rate
* Some kind of alignment protocol to correct any deviation, probably with wall alignment
* Maximize the documentation
* Fix any lingering problems from last years and make the robot overall more reliable

After this we searched up the most successful teams from last years and assigned everyone one or two documentations from those teams to review. This was really useful for us, since a lot of teams had great and interesting ways to solve this challenge, while also **learning what was required in the documentation** from analyzing the points they had gotten.

## The development phase

The most important tasks we wanted to tackle first were the camera and the differential, since without these parts the robot couldn't even start moving.

### The camera

In the last year's design we used a Pixy Ai camera to do the color detection for us. After a lot of tinkering it worked well enough for that season, but we found the camera to be a bit colorblind, so this year **we decided to take matters into our hands.**
Finding the right camera was the easiest part. We only had a few things we required. A large enough FOV, flat/non fisheye lenses and relatively easy integration. After just a bit of searching we landed on the **Raspberry Pi Camera Module 3.**
This camera had everything we needed. A FOV of 66° horizontal and 41° vertical. Since we use a Raspberry Pi 5 as the brain of our robot and this is the official camera made for the Raspberry Pi, integration was easy as Pi(e). There was already a fully feature complete Python library made for it and the Raspberry even has a dedicated camera port.
After this, we moved on to making the camera actually work. Making simple pictures was quite an easy task, but then it got a lot harder. First we had to test out the perfect height and angle the camera would need to be in order to get the right image.
angle and height tests
This took quite a few tries but we found a 15° depression angle at a height of around 20 cm to be sufficient for our needs. These measurements allowed us to make a 3D printed camera stand that would hold the camera in the right place. Then came the logic of the camera.
Our idea was to use the measurements from our **Lidar sensor to pinpoint the location of the obstacle** on the camera and then take the average of all the pixels inside that area thus getting a value of how green and how red it is. This is why it was important that we used a flat lense, since this way we didn't have to account for camera distortion and could avoid using matrix equations, allowing us to use simple geometry for our solution. But even with this, there were problems we had to solve. For example only after a few weeks did we realize that the camera **wasn't using its maximum FOV,** which was crucial for our calculations. Other than this we also had to be mindful about any modifications we made since then we had to update the camera's height and angle in the code. After a lot of fiddling and optimizing, **it worked beautifully.** While still not perfect it was already miles ahead in reliability compared to the Pixy cam.

### The differential

The differential was also a big part of last year's project and it managed to sneak its way into this year's as well. While the Lego differential we used before worked fine, it wasn't the most secure thing in the world. The wheels had a lot of play and the transmission was far from ideal. The motor we used was quite powerful with more than enough torque than we would ever need so we could afford to lose some. Thus **we decided on making a custom differential** with a 1:1 transmission rate, a lot tighter tolerances and imbedded bearings to decrease friction and make things more secure.
Making a differential is a lot harder than just slapping some cogs together, It requires a lot of data and calculations. So first we needed to make an accurate mechatronic model of our system and use it to design the 3D models. The modelling wasn't an easy task either, since **all the components had to fit together perfectly** and we wanted to use the fiberglass lego axles from last year requiring it to be compatible with Lego, while also having a D shaft as an input. 
After printing out the models we made, sanding out things where needed and doing some assembly everything seemed to work great. This was a great addition to our robot, since it made everything more precise and allowed us to reach even faster speeds, providing an increase of about 1.4 times and the asymmetric design of the gears made it a lot more efficient.

### The new motor

While the new differential already provided us with a decent speed bump, **we wanted more.** We managed to get maximum points last year but our time was rather lacking compared to the other teams earning maximum points, so we knew we had to improve more. To further increase the speed of our robot we decided to get a new motor of the same kind we used before but with a better built in transmission. This change lowered our torque even further, but with the staggering 3 times speed boost it provided, we decided to take the trade. With change our maximum speed had reached **over 4.5 times what we had the previous year.**

### Parking

The parking was one of the main rule changes compared to last year. While the increased parking space was really useful, parallel parking still proved to be a lot more difficult than perpendicular parking. We first tried a method of basically wiggling our way out of the parking space, but that added a lot more complexity and was influenced too much by the play in the motor and wheels. To fix this we had to **heavily modify our steering gear,** by moving up the servo and extending its range to the absolute limit. These changes allowed the robot to simple drive out of the parking space with one turn.

driving mechanism changes

### Speeding up the Lidar

The refresh rate of our Lidar was already a problem last year and since the speed of our robot has increased even further this problem did as well. The problem stems from the fact that the Lidar only spins 10 times a second, meaning that a given degree only refreshes every 0.1 seconds, so if the robot were to move at a speed of 1.5 m/s then **the robot could move 15 cm between two measurements,** making the run a lot more instable. With some trial and error we managed to get it up **from 10 to 15 Hz** which is still quite slow, but a decent enough improvement.

### Wall alignment

We also needed some way to further stabilize the run. An issue that came up sometimes was that the gyro could slowly shift causing the robot deviate from how far we wanted it to be from the wall. We fixed it by adding a little correction arcing each time we went in a straight line. The arc was just small enough that it **could do it without moving the Lidar.** This change made the robot a lot more predictable and reliable.

### Predictive gyro

Just like Lidar, we had issues with the refresh rate of the gyro as well, but with turning. However we could use a more robust solution this time, since the gyro on outputs one value and that value cannot have big jumps in it. We decided on using an interpolation method, basically **predicting the gyro values based on previous data,** allowing us to end turns at just the right time.

### Troubleshooting

In the development process we also encountered some rather peculiar and informative issues. Those are listed below:

* We noticed some issues with the Lidar. First of all we noticed seemingly random 0 values appearing in our logs, that disappeared for some reason when we covered the robot with a box. Turns out when the light from the Lidar bounces away into world and does not return or goes further than 12 meters, the Lidar will say the distance was 0. Thankfully we could ignore those values. Another problem was the dead zone of the Lidar changing, but we could solve that by implementing dead zone management into our code.

* A problem with our motor also arose, when it started moving in an uneven throbbing fashion, that disappeared when we stopped controlling it. This was most likely caused by electromagnetic interference from one of the cables near the motor. After moving the cables, the problem disappeared.

* After the speed increase the tires of the robot started sliding a bit when braking and starting. This was easily fixed by replacing the back tires with ones that have more grip.

* When replacing the motor, we didn't account for the fact that it had a slightly shorter shaft, which later caused the cog to slip off from it. Fortunately the fix was just making the back of the cog a bit longer. 

### Aesthetic changes

When working on the robot we realized a grave mistake we had made last year. **We did not give a name to our robot,** so we needed to change that as soon as possible. Since during testing our robot had a tendency tu bulldoze over things, we decided on naming it Dózer, from the word bulldózer, which just means bulldozer. After coming up with the name we also wanted it to look the part, so we gave it a little shovel upfront and a license plate on the back.

---

## Optimizing and the finishing touches

The changes we made up till this point were made before the national competition as these were the bulk of what we had planned. While not changing the look of the robot that much, these changes were still astronomical when it came to how the robot functions. These changes turned out great, however things like these **still needed a lot of polishing.** So once the national final has ended and we finally got some rest, we sat out once again to finally complete the robot. While there were no more huge changes that needed to be made, there were still things that required small improvements to be perfect. Just like before, we made a list of the things that we had to work on:

### New motor controller

The first change we made was getting a new motor controller. While the previous one worked fine, it was quite big and inefficient, so we decided to get a new one. **The new one solved those issues and even made our robot go a lot quiter.**

### Custom interconnect PCB

In order to save some space and ensure proper
wiring, we designed a custom PCB in [KiCad](https://www.kicad.org/). We had already made something similar before, but we decided to make a more sophisticated one this time around.
The PCB is designed to
house the ESP, and make connencting it to the other systems and parts of the robot a lot simpler and more intuitive.

PCB render

Two mounting holes were added to allow us to affix the PCB using 2 M3 screws. In order to save some space, we also added a few redundant pins to the `GYRO1` element. This let us put the IMU right on the top of the PCB.

As a safety precaution and to ensure extensibility, all ESP pins were mirrored to their respective sides. This proved essential, because we failed to notice a critical mistake before ordering the PCB. ENC1 and ENC2 were 1 pin higher (below the +3V3 label), meaning that instead of ENC1 being connected to a programmable GPIO pin, it connected to the EN pin. This meant that, whenever the pin got any power, the enable pin triggered a reset in the ESP. While we lacked the time to order a new PCB before the competition, we could use a jumper connected to one of the pin mirrors to amend this issue. As for the files themselves, all PCB design documents contain a version where this wiring mistake has been fixed.

After every factor mentioned above has been dealt with, a BOM assembled, and the PCB ordered, the PCB was successfully integrated into the car (besides the EN miswiring mentioned above).

### Filtering out errors in the raspberry - esp communication system

Communication between the computing units was always a tricky part. There were always a lot of things that could go wrong. While most of the problems we encountered were fixed by this point, there was always a chance that any data we sent could get corrupted by the time it has reached its goal. We eased this problem by **integrating a checksum into our communication system,** which in short checks the sum of the message on both sides and compares them, thus being able to tell if the message was corrupted in any way.

### Optimizing robot path to improve speed

Last year, our main focus was stability, while this year we also decided to focus on speed. While stability is still the most important aspect of the robot, we realized that also needed to shave off from the runtime as much as we could in order to not fall behind in the competition. We already massively improved the speed of the robot, but we knew that we could also gain time by just making it go a shorter distance. Previously this seemed impossible as there were problems with our turning angle, but we managed to **tweak some things in our turning gear, finally making this possible.** Now the robot can optimize its path even more making it that sometimes even one short turn is enough for entire sections of the map.

### Fine-tuning the sensors

The sensors are the eyes of the vehicle, so it was always very important that they worked "well", but that "well" part **could only be called "well enough" up to this point.** To change this we had to implement a few things.

First of all, we found that there was a proportional error in our IMU. Thankfully this was a constant value, so there was a constant difference in every 360 degrees, meaning that it was something that our ESP could handle easily by adjusting for it.

Then we also fixed the problem caused by the misalignment of the lidar and the camera. The solution was to check their angle compared to the straight axis (which is the axis perpendicular to the rear/driving axis of the car) and make a slight correction according to it.

Finally, to make finding problems easier in the future, we also added a few features to our debbuging program, like also implementing the camera images into the playback feature, and adding a menu to create different run presets to streamiline the testing process.

### Improving the wheels

The final thing we did was to change out the wheels. The wheels we were using at that time worked flawlessly, however with the robot being able to go much faster, they had started to slip. We could have just changed them to a bigger wheels with more grip, but that could have posed a problem when parking. Luckily we managed to find a pair of wheels **that fit both criteria of being thin and grippy,** so we started using those instead. After this the only thing left to fix was making them mount better on the front, since there we used screws for mounting, instead of an axle. For this we edited the 3d model of the rim, so that it could have **a nut inserted inside of it.** We did have to make a few versions of this design, since the first one did not turn out so well, but we did end up making a good one. These fixes were the last things we needed to do to complete the robot, and after doing so, the robot ended up working beautifully.

evolution of our robot

---

## Teamwork

We usually **met up once a week to work on this project,** but even when we weren't together we would work on it. We kept a log of all the times we worked on something. Everyone had a part of this project that they were the most familiar with, and so when we were not together we would usually work on those parts and then share our code snippets and unfinished or work in progress documentation via a private GitHub, finally publishing it on the official one. Any chance we got we would talk or text about what to do, what we should focus on, frequent communication was a key part of our work. We needed to have a clear goal every time in order to not get sidetracked and waste our time on the unimportant things. Every week when we met up, first we merged everything we did separately together and then did the things that all of us were needed for. This way even though we only met up once a week, **we could have a constant flow of progress.** It's important that even though every member of our team had an area of the project they were most familiar with, we still strived to introduce each other ot our own areas, so that everyone is familiar with the whole project as a whole. We believe this is necessary for efficient teamwork.

## The future

We made huge improvements over last year, making the robot a lot faster and more reliable, making us very hopeful for this year's competition. While this is as good as the robot has ever been, we will always find new things to improve on. But for us to know what we truly need to change, **we first need to wait until we can learn about the next year's challenge,** until then, we can only keep planning.

## Conclusion

Overall we are **incredibly happy with how our robot turned out** and glad we took upon this challenge and went on this journey together. We could successfully do all the things we had planned and even made some funny memories in the process. The process was hard, but worth it in the end and we hope to continue working on it in the future.

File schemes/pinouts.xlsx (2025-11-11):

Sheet: PI
EMERGENCY START
 |  |  | LIDAR VCC
 |  |  | LIDAR GND
EMERGENCY START
 |  |  | LIDAR UART TXD
L&K VCC
Buzzer -
Buzzer +
L&K CLK
L&K DIO |  |  | L&K STB
L&K GND
ESP UART TX | W | USB UART RX
ESP UART RX |  | USB UART TX

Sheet: ESP32
(IMU VCC) | D | ! ENC1 VCC |  | (IMU PS0) | D |  | PSU GND | (SERVO GND) | D | (IMU GND)
 |  |  | ! | ENC_1 A | W
 |  |  | ! | ENC_1 B |  |  | LiDAR PWM |  | -
 |  |  |  | UART (PI) RXD
 |  |  |  | UART (PI) TXD | W
 |  |  |  | Servo PWM | W | D | IMU_RXD
 |  |  |  |  |  |  | Motor_PWM2
 |  |  | ! | ENC1 GND
 |  |  |  | Motor_PWM1
 |  | (Servo VCC) |  | PSU 5V

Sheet: ESP Board new
 |  | Jumper A | Jumper A | PI TX | PI RX
 |  | D |  |  | W
 |  |  |  |  |  | D | IMU
LiDAR PWM
VCC | W
GND
 | -
 | -
 | - |  |  |  |  |  | Motor PWM1
 | - |  |  |  |  |  | Motor PWM2
Servo GND
Servo VCC
Servo PWM | W

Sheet: M ctrl
 |  | - | -
GND IN
12V IN
 |  |  |  | Motor_PWM1
M+ |  |  |  | Motor_PWM2
M- | W

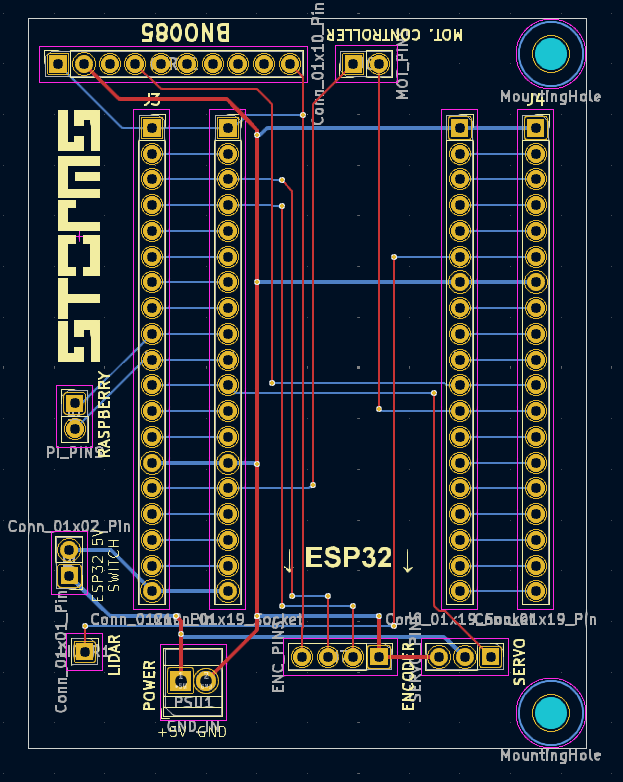
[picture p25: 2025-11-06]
schemes/PCB_design.png

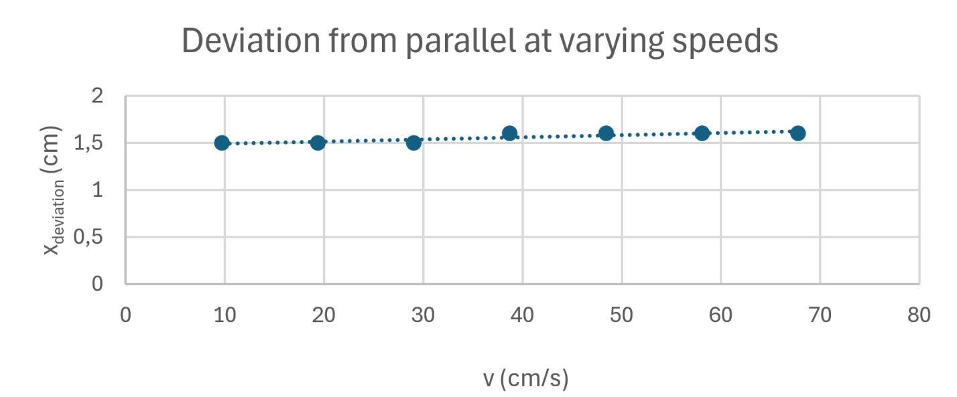
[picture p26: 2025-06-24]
parallel.webp

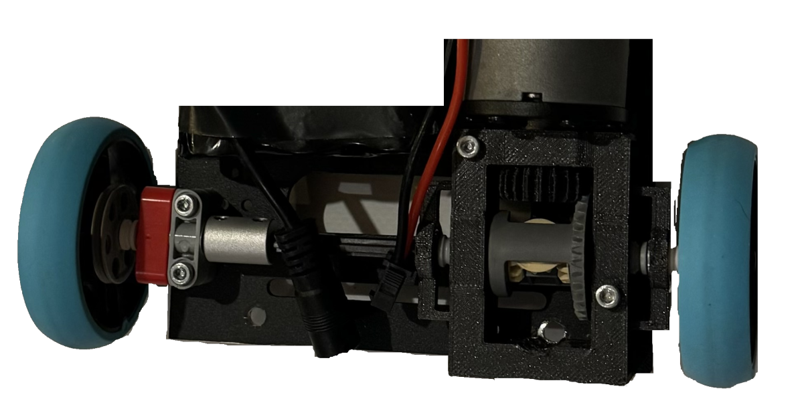
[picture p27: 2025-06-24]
diff.webp

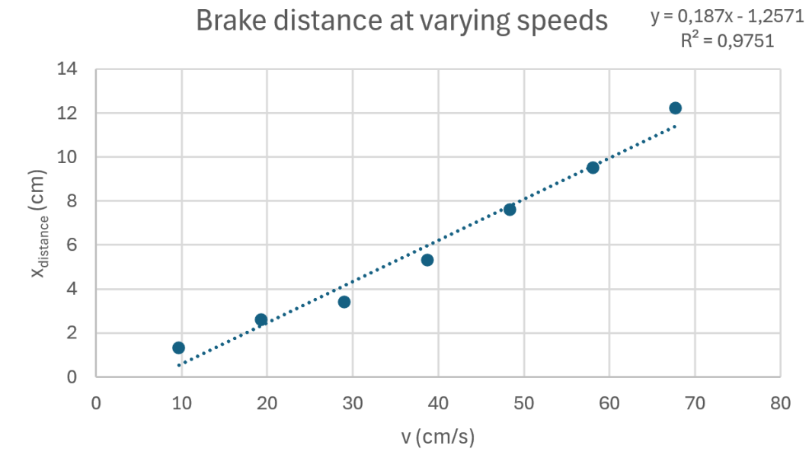
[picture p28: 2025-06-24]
break.webp

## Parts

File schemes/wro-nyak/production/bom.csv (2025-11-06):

Designator | Footprint | Quantity | Value | LCSC Part #
GYRO1 | PinSocket_1x10_P2.54mm_Vertical | 1 | Conn_01x10_Pin | C57369
J1, J2 | PinSocket_1x19_P2.54mm_Vertical | 2 | Conn_01x19_Socket | C2897382
J3, J4 | PinSocket_1x19_P2.54mm_Vertical | 2 | Conn_01x19_Pin | C2897382
J5 | PinHeader_1x02_P2.54mm_Vertical | 1 | PI_PINS | C2905434
J6 | PinHeader_1x02_P2.54mm_Vertical | 1 | MOT_PINS | C2905434
J7 | PinHeader_1x04_P2.54mm_Vertical | 1 | ENC_PINS | C2905435
J8 | PinHeader_1x03_P2.54mm_Vertical | 1 | SERVO_PINS | C2932698
J9 | PinHeader_1x02_P2.54mm_Vertical | 1 | Conn_01x02_Pin | C2905434
LIDAR1 | PinHeader_1x01_P2.54mm_Vertical | 1 | Conn_01x01_Pin | C81276
PSU1 | TerminalBlock_Xinya_XY308-2.54-2P_1x02_P2.54mm_Horizontal | 1 | GND_IN | C5188442

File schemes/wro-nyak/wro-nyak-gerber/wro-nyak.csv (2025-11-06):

Id | Designator | Footprint | Quantity | Designation | Supplier and ref
1 | PSU1 | TerminalBlock_Phoenix_MPT-0,5-2-2.54_1x02_P2.54mm_Horizontal | 1 | GND_IN
2 | GYRO1 | PinSocket_1x10_P2.54mm_Vertical | 1 | Conn_01x10_Pin
3 | J8 | PinHeader_1x03_P2.54mm_Horizontal | 1 | SERVO_PINS
4 | J2,J1 | PinSocket_1x19_P2.54mm_Vertical | 2 | Conn_01x19_Socket
5 | J5 | PinHeader_1x02_P2.54mm_Vertical | 1 | PI_PINS
6 | J4,J3 | PinSocket_1x19_P2.54mm_Vertical | 2 | Conn_01x19_Pin
7 | J6 | PinHeader_1x02_P2.54mm_Vertical | 1 | MOT_PINS
8 | J7 | PinHeader_1x04_P2.54mm_Horizontal | 1 | ENC_PINS
9 | LIDAR1 | PinHeader_1x01_P2.54mm_Horizontal | 1 | Conn_01x01_Pin

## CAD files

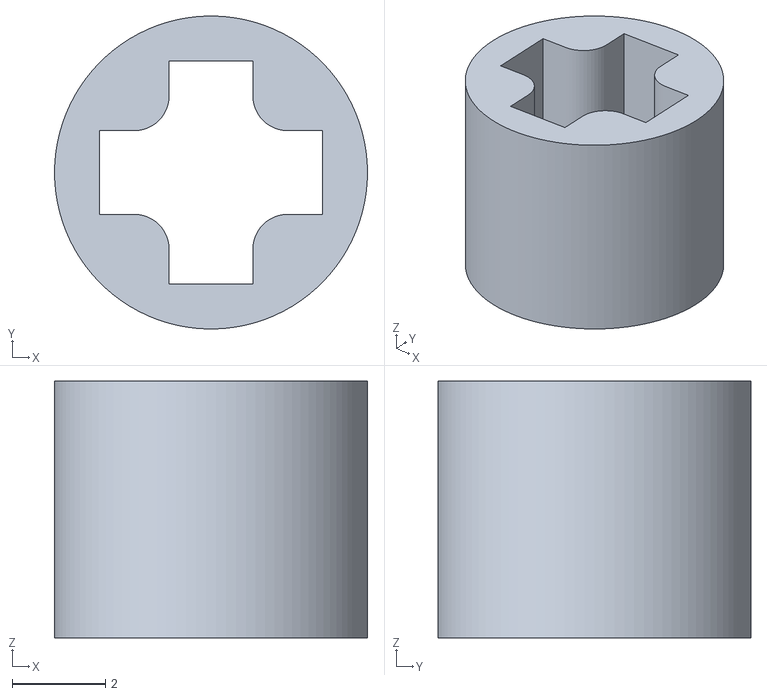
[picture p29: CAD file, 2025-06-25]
models/ring.stl
6.70 x 6.70 x 5.50

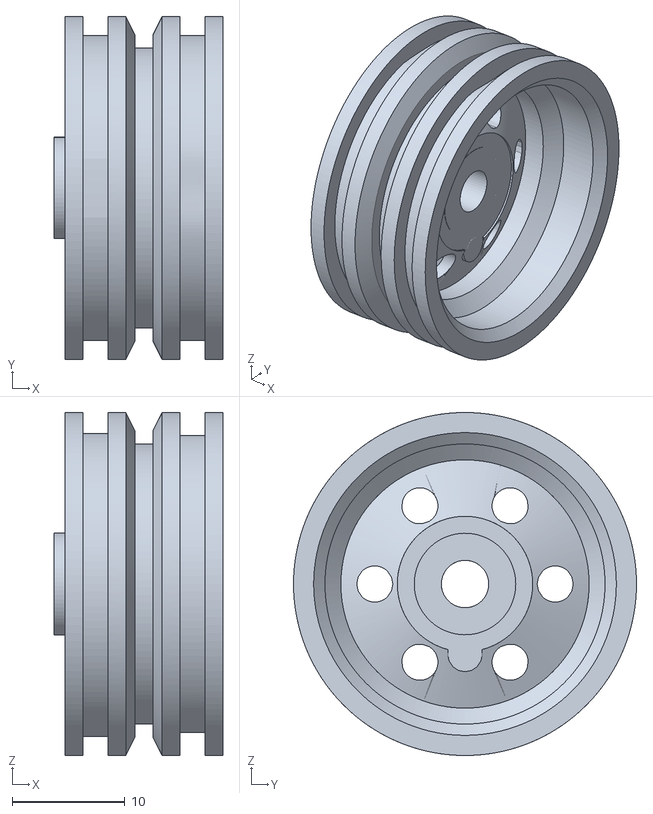
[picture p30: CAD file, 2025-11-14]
schemes/nutted wheel.stl
15.0 x 30.4 x 30.4

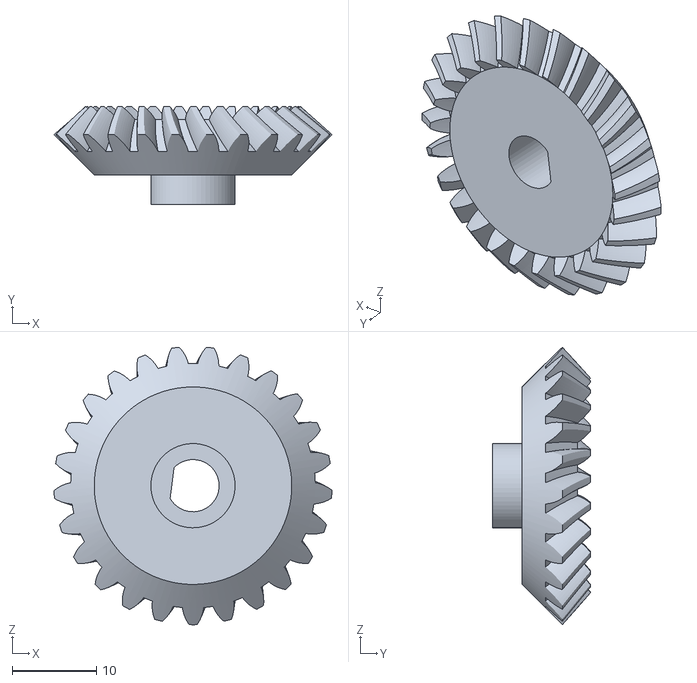
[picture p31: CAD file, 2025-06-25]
models/diff cog.stl
33.0 x 11.6 x 32.9

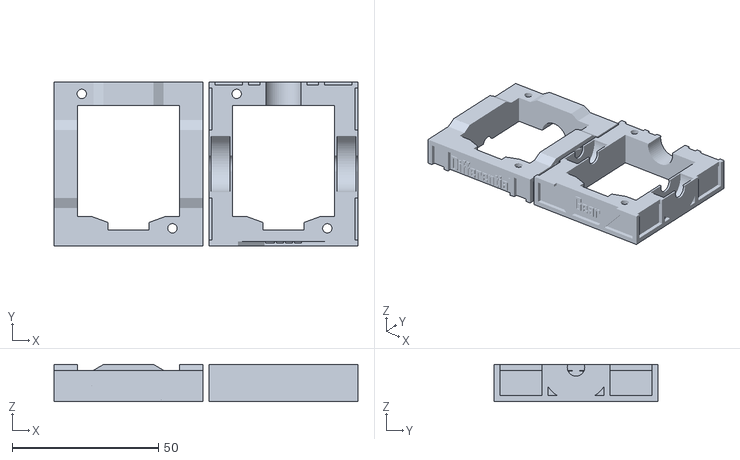
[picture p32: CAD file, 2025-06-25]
models/diff frame.stl
104.0 x 56.0 x 12.7

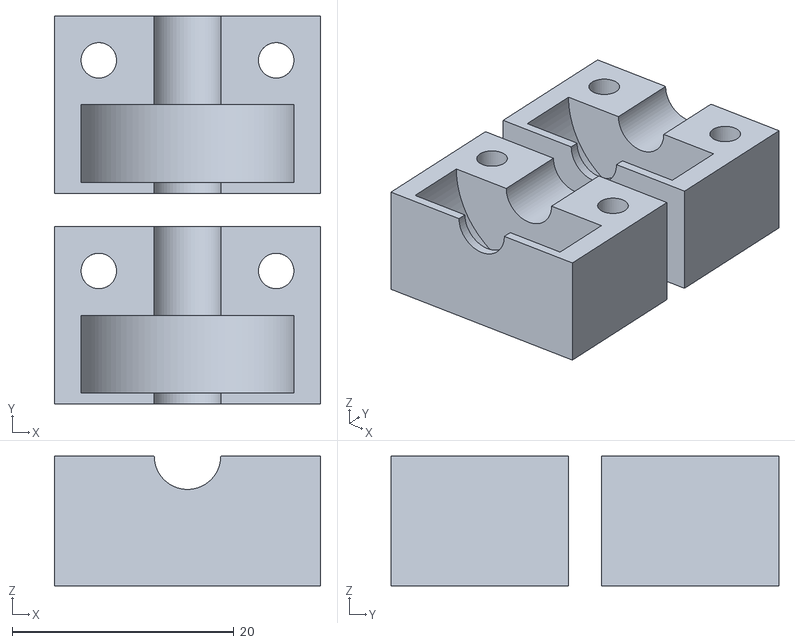
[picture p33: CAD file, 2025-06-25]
models/axle holder.stl
24.0 x 35.0 x 11.7

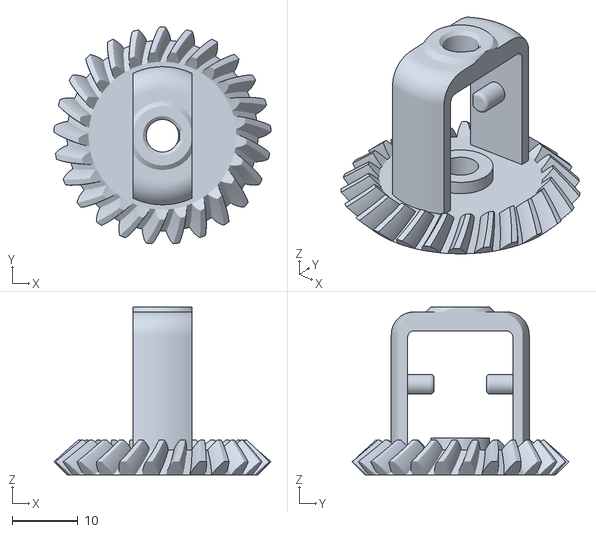
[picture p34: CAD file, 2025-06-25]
models/diff.stl
33.0 x 32.9 x 25.5

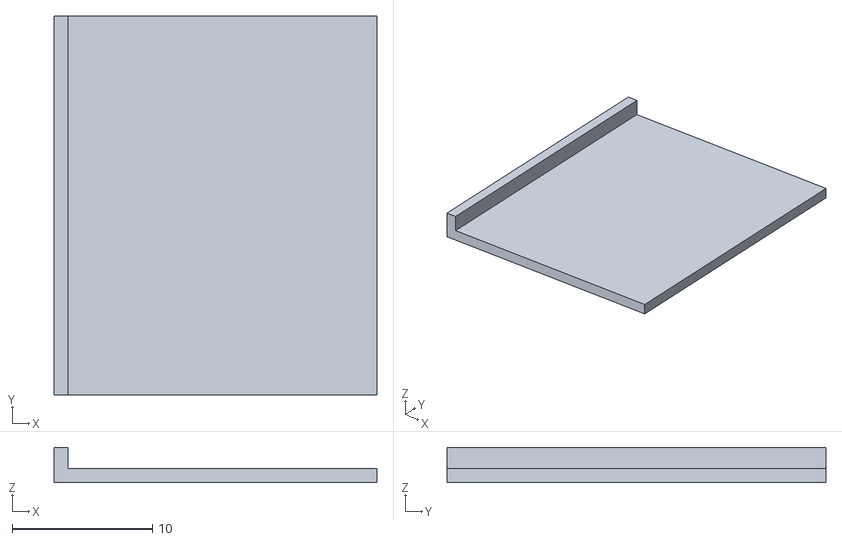
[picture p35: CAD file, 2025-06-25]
models/lid.stl
23.0 x 27.0 x 2.50

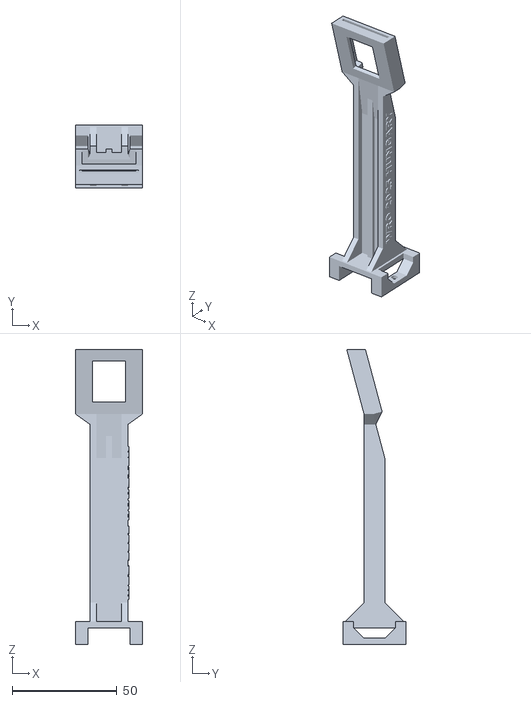
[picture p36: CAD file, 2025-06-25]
models/Camera final.stl
32.0 x 30.0 x 141.1

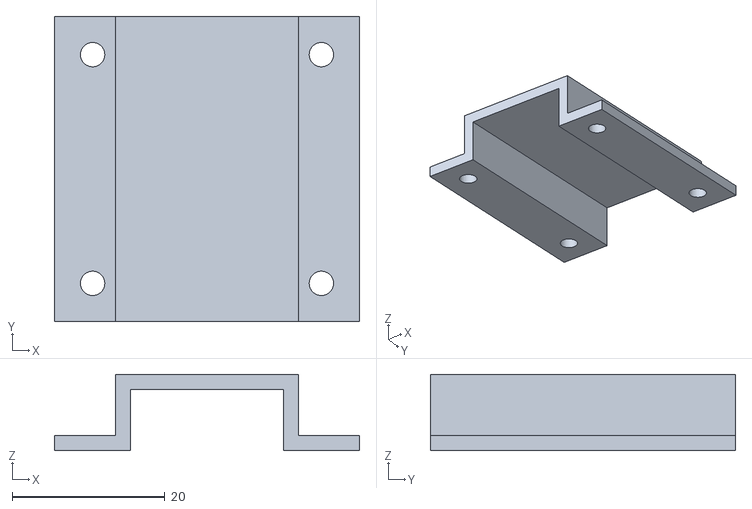
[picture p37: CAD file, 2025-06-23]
models/tunnel.stl
40.0 x 40.0 x 10.0

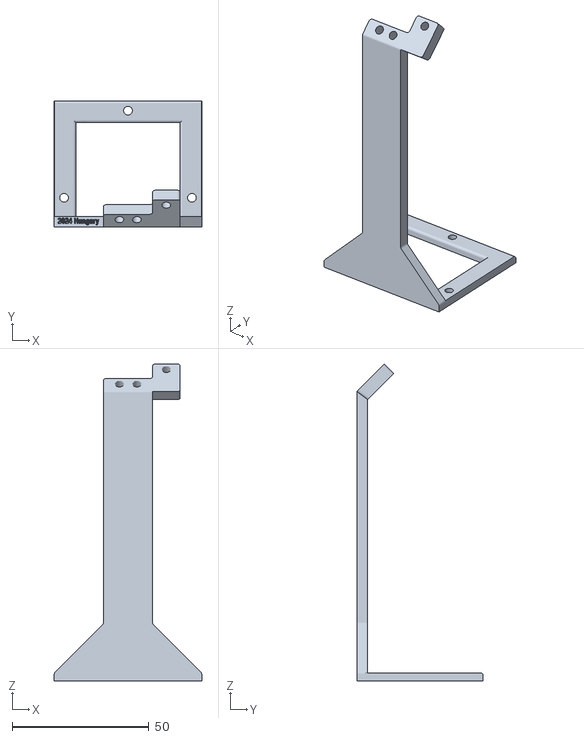
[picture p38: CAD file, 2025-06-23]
models/Camera stand.stl
54.0 x 46.3 x 116.0

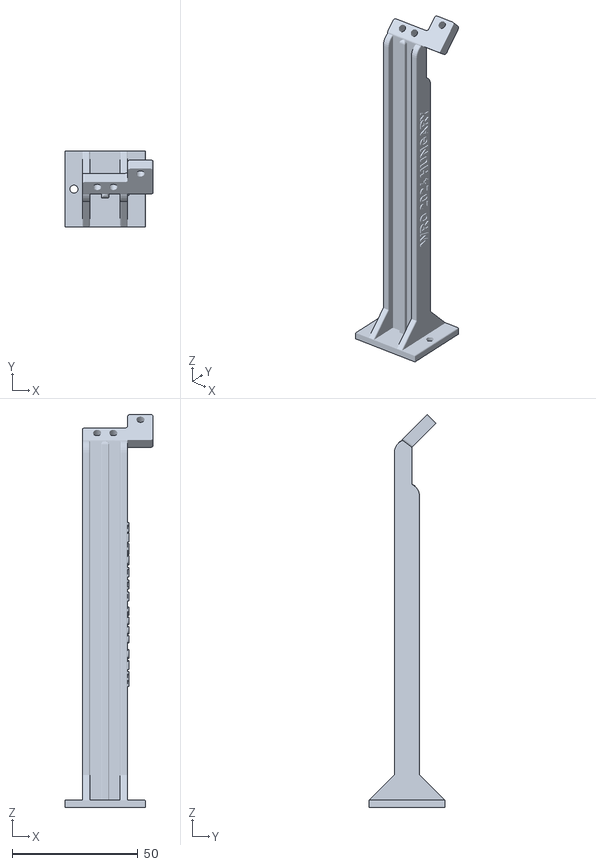
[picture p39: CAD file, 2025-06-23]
models/Camera stand 3 v2.stl
35.1 x 30.0 x 156.0

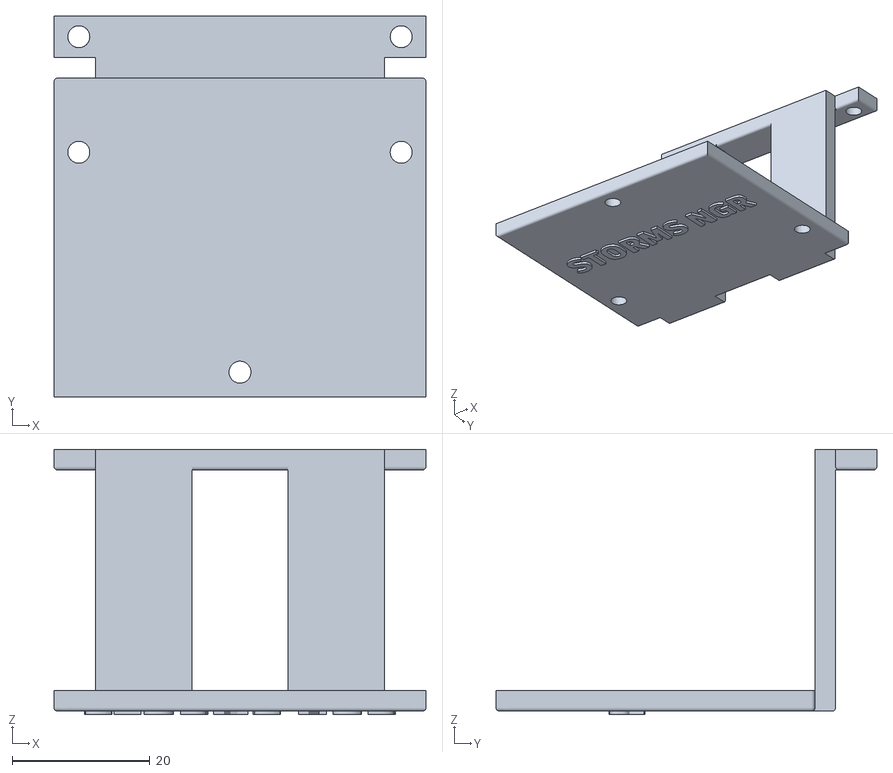
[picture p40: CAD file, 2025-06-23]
models/Lidar stand.stl
54.0 x 55.3 x 38.5

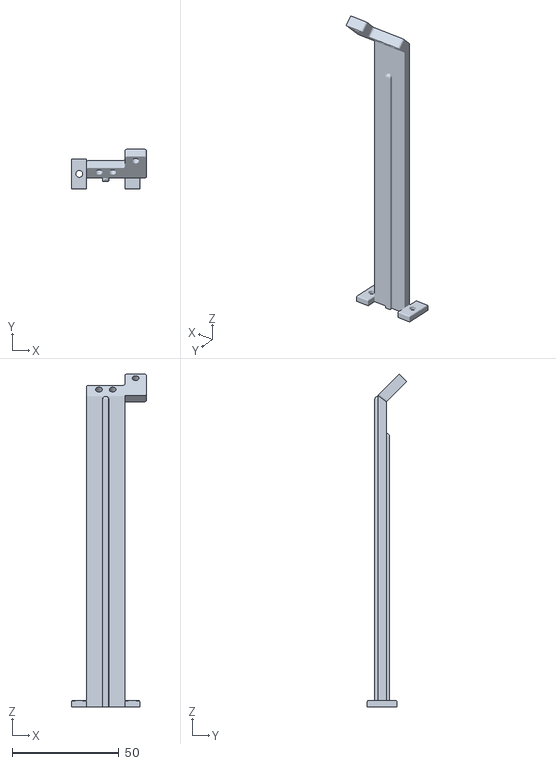
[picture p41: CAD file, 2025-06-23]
models/Camera stand 2 v1.stl
35.1 x 18.5 x 156.0

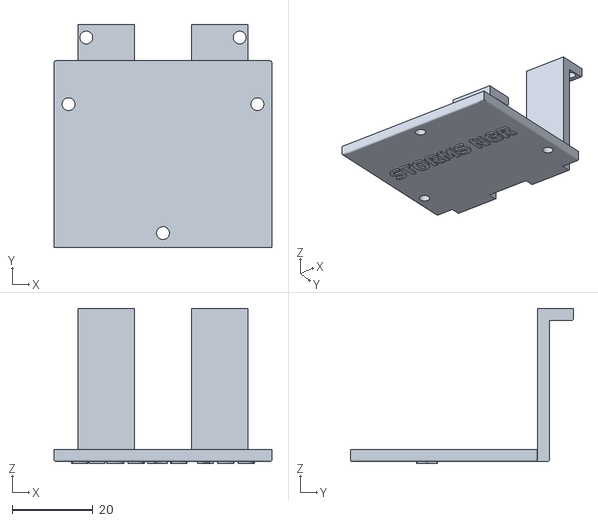
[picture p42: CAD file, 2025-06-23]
models/Lidar mount.stl
54.0 x 55.3 x 38.5

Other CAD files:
schemes/wheel original.stl
models/Camera stand 3 v1.stl
models/Camera final.f3d
models/Camera stand 2 v1.f3d
models/Camera stand 2 v2.f3d
models/Camera stand 2 v3.f3d
models/Camera stand.f3d
models/Lidar mount.f3d
models/Lidar_mount.f3d
models/axle holder.f3d
models/diff cog.f3d
models/diff frame.f3d
models/diff.f3d
models/lid.f3d
models/ring.f3d
models/tunnel.f3d
schemes/nutted wheel.f3d

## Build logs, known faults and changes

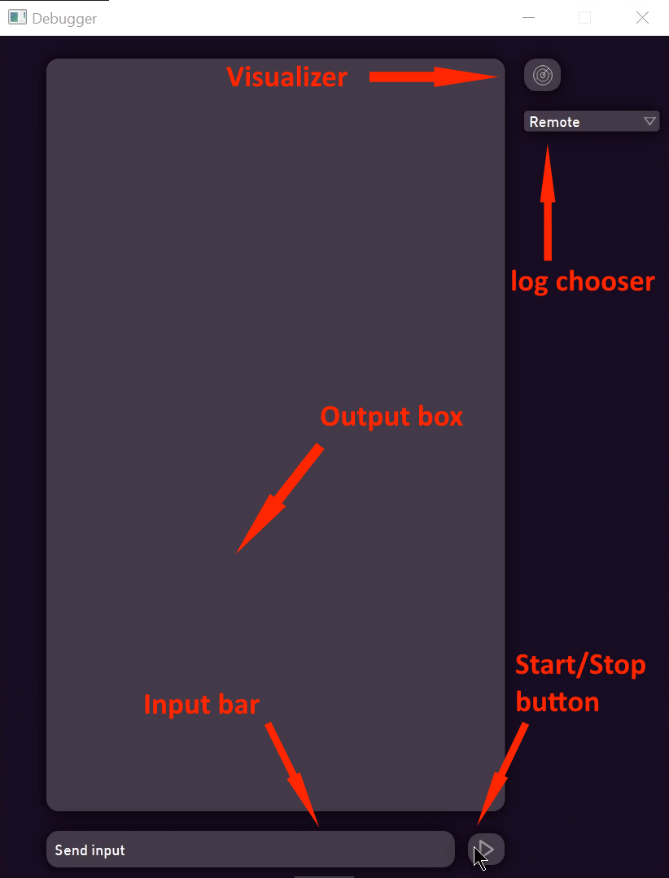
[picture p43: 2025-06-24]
other/RpiCode/Debugger.png

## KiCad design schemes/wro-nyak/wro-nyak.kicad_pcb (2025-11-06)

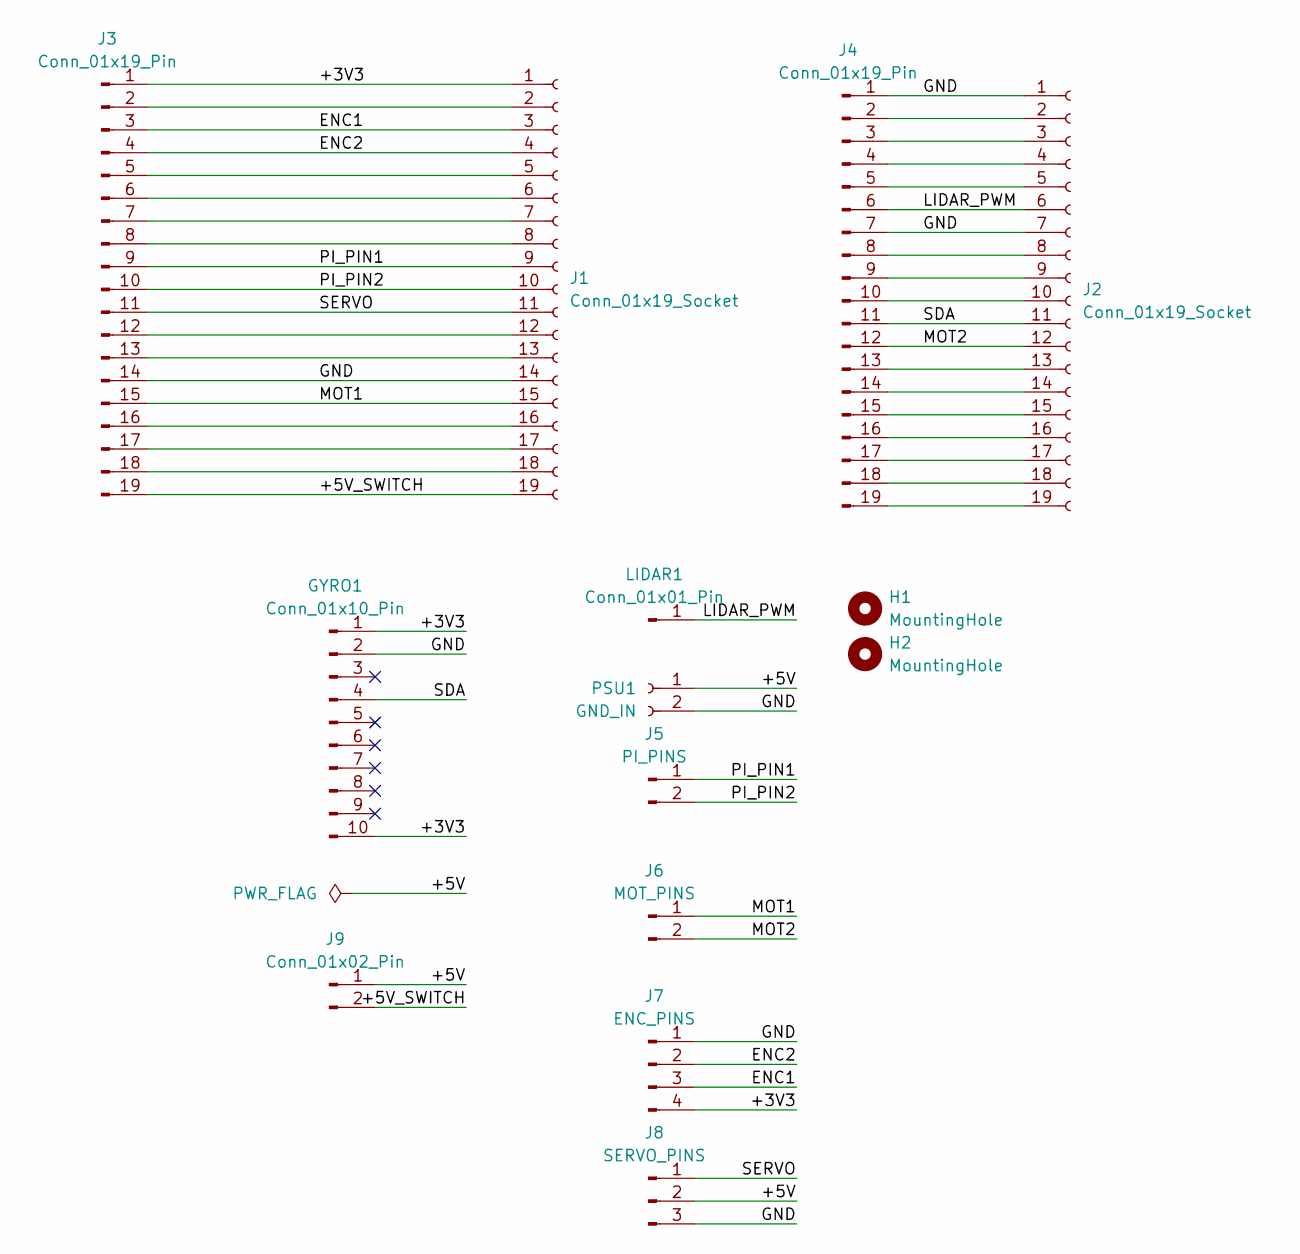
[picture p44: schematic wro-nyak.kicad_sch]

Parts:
GYRO1: Conn_01x10_Pin; PinSocket_1x10_P2.54mm_Vertical; LCSC C57369
H1, H2: MountingHole; MountingHole_3.2mm_M3
J1, J2: Conn_01x19_Socket; PinSocket_1x19_P2.54mm_Vertical; LCSC C2897382
J3, J4: Conn_01x19_Pin; PinSocket_1x19_P2.54mm_Vertical; LCSC C2897382
J5: PI_PINS; PinHeader_1x02_P2.54mm_Vertical; LCSC C2905434
J6: MOT_PINS; PinHeader_1x02_P2.54mm_Vertical; LCSC C2905434
J7: ENC_PINS; PinHeader_1x04_P2.54mm_Vertical; LCSC C2905435
J8: SERVO_PINS; PinHeader_1x03_P2.54mm_Vertical; LCSC C2932698
J9: Conn_01x02_Pin; PinHeader_1x02_P2.54mm_Vertical; LCSC C2905434
LIDAR1: Conn_01x01_Pin; PinHeader_1x01_P2.54mm_Vertical; LCSC C81276
PSU1: GND_IN; TerminalBlock_Xinya_XY308-2.54-2P_1x02_P2.54mm_Horizontal; LCSC C5188442

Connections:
/+3V3: GYRO1.1, GYRO1.10, J1.1, J3.1, J7.4
/+5V: J8.2, J9.1, PSU1.1
/+5V_SWITCH: J1.19, J3.19, J9.2
/ENC1: J1.3, J3.3, J7.3
/ENC2: J1.4, J3.4, J7.2
/GND: GYRO1.2, J1.14, J2.1, J2.7, J3.14, J4.1, J4.7, J7.1, J8.3, PSU1.2
/LIDAR_PWM: J2.6, J4.6, LIDAR1.1
/MOT1: J1.15, J3.15, J6.1
/MOT2: J2.12, J4.12, J6.2
/PI_PIN1: J1.9, J3.9, J5.1
/PI_PIN2: J1.10, J3.10, J5.2
/SDA: GYRO1.4, J2.11, J4.11
/SERVO: J1.11, J3.11, J8.1
unnamed: J1.2, J3.2
unnamed: J1.5, J3.5
unnamed: J1.6, J3.6
unnamed: J1.7, J3.7
unnamed: J1.8, J3.8
unnamed: J1.12, J3.12
unnamed: J1.13, J3.13
unnamed: J1.16, J3.16
unnamed: J1.17, J3.17
unnamed: J1.18, J3.18
unnamed: J2.2, J4.2
unnamed: J2.3, J4.3
unnamed: J2.4, J4.4
unnamed: J2.5, J4.5
unnamed: J2.8, J4.8
unnamed: J2.9, J4.9
unnamed: J2.10, J4.10
unnamed: J2.13, J4.13
unnamed: J2.14, J4.14
unnamed: J2.15, J4.15
unnamed: J2.16, J4.16
unnamed: J2.17, J4.17
unnamed: J2.18, J4.18
unnamed: J2.19, J4.19

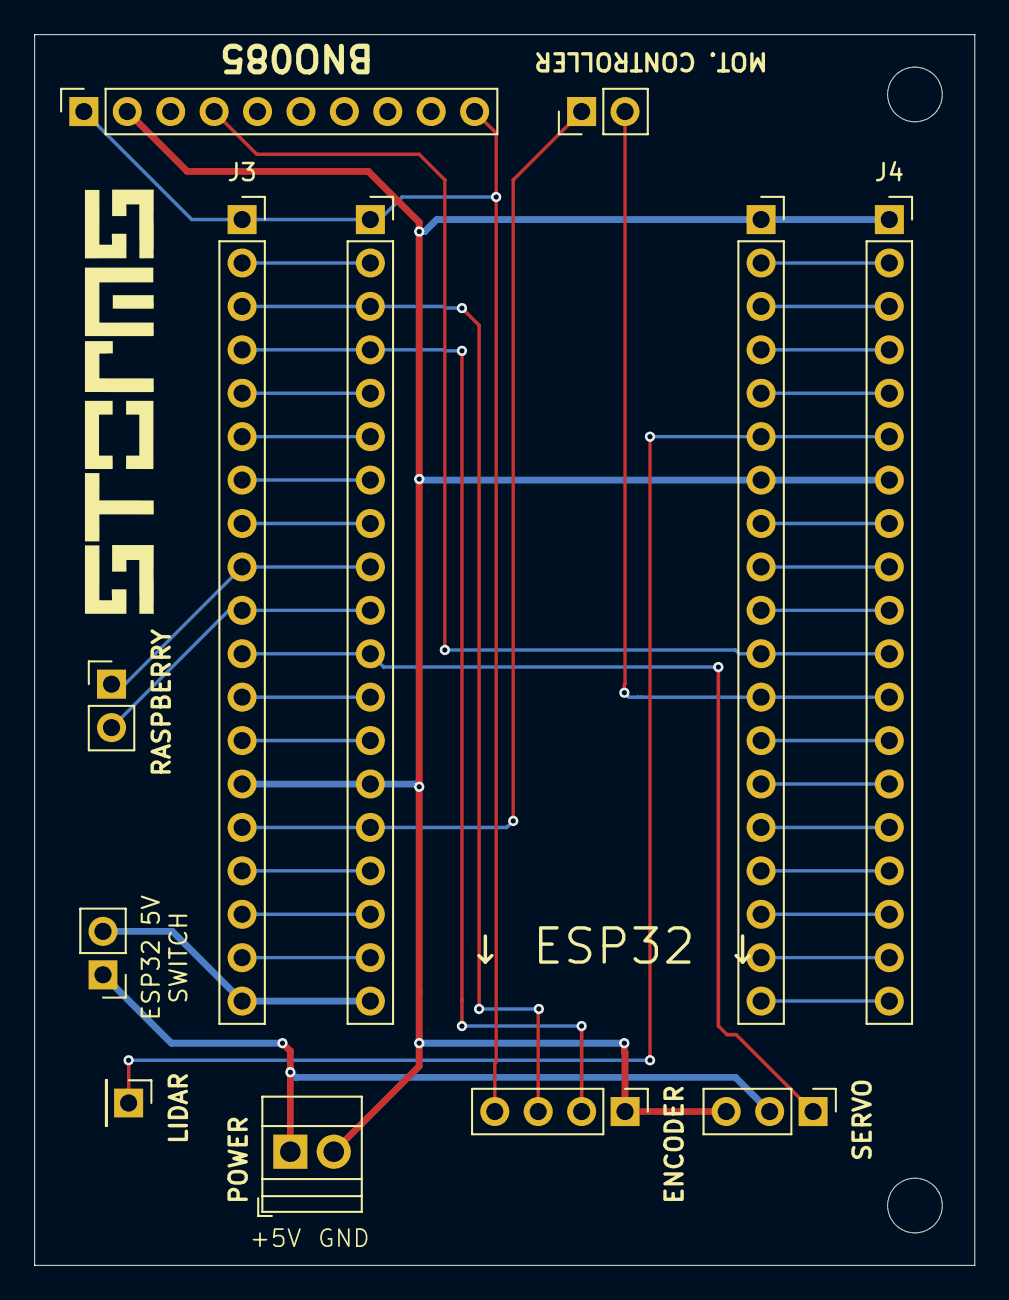
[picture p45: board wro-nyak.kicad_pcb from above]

Board: 2 copper layers, 55.0 x 72.0 mm, 14 parts (0 on the bottom side), 37 nets.

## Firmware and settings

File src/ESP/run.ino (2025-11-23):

#include <cmath>
#include <Wire.h> //I2C communication library
#include "Adafruit_BNO08x_RVC.h" //Gyroscope library

#define B_PIN_L 36 //Left motor encoder A pin
#define A_PIN_L 39 //Left motor encoder B pin
// #define PWM_PIN_L 21 //Left motor PWM pin (speed control)
#define PWM_BW_PIN 16 //Backward PWM pin
#define PWM_FW_PIN 13 //Forward PWM pin
#define A_PIN_R 35 //Right motor encoder A pin
#define B_PIN_R 34 //Right motor encoder B pin
// #define PWM_PIN_R 16 //Right motor PWM pin (speed control)
#define LED_PIN 2 //Built-in Led on the ESP
#define S_PWM_PIN 27 //Servo PWM pin (turning)
#define SRL_TX_PIN 25 //Serial communication TX pin (with raspberry)
#define SRL_RX_PIN 26 //Serial communication RX pin (with raspberry)
#define IMU_RX_PIN 17 //Serial communication receive pin (gyroscope)
#define IMU_TX_PIN 32 //Serial communication transmit pin (gyroscope)
#define US_TRIGGER_PIN -1 //Ultrasonic sensor trigger pin (send soundwave) (NOT CONNECTED)
#define US_ECHO_PIN -1 //Ultrasonic sensor echo pin (on measurement done) (NOT CONNECTED)
#define LIDAR_PWM_PIN 21 //LiDAR pwm speed control pin (18)


#define spwm_freq 50 //servo PWM frequency
#define spwm_res 12 //servo PWM resolution (2^12)
// #define spwm_channel 0 //servo PWM channel
#define motor_pwm_freq 19000 //motor PWM frequency

#define motor_pwm_res 12 //motor PWM resolution (2^12)

#define lidar_pwm_res 12 //lidar speed PWM resolution (2^10)
#define lidar_pwm_freq 1000 //lidar speed PWM frequency
#define LIDAR_PWM_SLOW 2211 //middle


#define I2C_ADDRESS 0x8 //I2C address of this ESP device

//Commands: These are used in the communication between the ESP and the raspberry
#define CMD_SYNC 17 //Synchronization command (raspberry)
#define CMD_STEER  6 //Steering command
#define CMD_HEARTBEAT 7 //Heartbeat command signal
#define CMD_LOG 8 //(retrieve)Log command
#define CMD_SET_VMODE 9 //set vmode (velocity mode) command
#define CMD_SET_TARGETSPEED 10 //set target speed command
#define CMD_SET_SMODE 18 //set smode (steer mode) command
#define CMD_SET_BREAKPERCENT 19 //set breaking percentage command
#define CMD_SET_TARGET_YAW 20 //set target yaw (heading) command
#define CMD_SET_SERVO_MAX 21 //set the maximum servo state
#define CMD_SET_SERVO_MIN 22 //set the minimum servo state
#define CMD_SET_SERVO_CENT 23 //set the central servo state
#define CMD_SET_UNREG 25 //set unregulated motor power
#define CMD_SET_GYRO_P 26 //set straightkeeping p parameter
#define CMD_SET_GYRO_D 27 //set straightkeeping d parameter
#define CMD_SET_SPCTRL_P 28 //set speed control p parameter
#define CMD_SET_SPCTRL_D 29 //set speed control d parameter
#define CMD_SET_HANDBRAKE_P 30 //handbrake vmode p parameter
#define CMD_SET_HANDBRAKE_I 31 //handbrake vmode i parameter
#define CMD_SET_ARCDIR 32 //send arc direction
#define CMD_SET_GYRO_L_MILLIS 33 //set arc prediction millis
#define CMD_SET_SGYRO_LIMITS 34 //set smode gyro limits
#define CMD_SET_SPCTRL_I 35 //set speedcontrol i parameter
#define CMD_SET_GYROERROR 36 //set gyro error compensation value
#define CMD_SET_ARCCANCEL 37 //force stop arc

#define CMD_DATA_POSL 11 //retrieve left motor position command
#define CMD_DATA_POSR 12 // retieve right motor position command
#define CMD_DATA_POSAVG 13 // retieve average motor position command
#define CMD_DATA_VMODE 14 // retrieve vmode command
#define CMD_DATA_SPEED 15 // retieve current speed command (real speed, not target)
#define CMD_DATA_ABS_GYRO 16 //retieve "absolute" gyro (does not loop back after 180 degrees to -180)
#define CMD_DATA_US 24 //retieve ultrasonic sensor measaured distance

#define US_DELAY 50 //Ultrasonic sensor delay (how much delay should be between sensor readings in milliseconds)

#define LED_C 15 //led PWM channel, not used

#define SYNC_CODE 18 //synchronization command response

#define STATUS_SYNCING 1 //ESP is trying to sync with raspberry pi
#define STATUS_CONNECTED 2 //ESP is successfully connected to raspberry pi

#define PiSerial Serial1

//VModes (velocity modes)
#define V_FORWARD 1 //robot is moving forward
#define V_BACKWARD -1 //robot is moving backward
#define V_STOP 0 //robot is stationary
#define V_BRAKE -2 //robot is braking (counter drive)
#define V_UNREGULATED 2 //the motors are powered with a constatnt force without speed control
#define V_HANDBRAKE -3

//SModes (steer modes)
#define S_NONE 0 //no steering
#define S_GYRO 1 //gyro controlled steering (keeping the robot straight)
#define S_ARC 2 //turn until target angle has been reached

//PID constants for dribing the motors
int kP=2; //UP
int kI=0;
int kD=0;

//PID constants for steering
int kPY=5;
int kIY=0;
int kDY=0;

int SERVO_MIN=219; //maximum safe left state servo PWM
int SERVO_MAX=417; //maximum safe right state servo PWM
int SERVO_CENT=291; //calibrated central state servo PWM

int conn_state=STATUS_SYNCING;
int heartBeatT0=0; //last heartbeat time

int posL=0;
int posR=0;
// int posAvg=0;
int lastTicks=0;
int speed=0;
int targetSpeed=0;
int brakePowerPercent=10;
int unregPower=0;

volatile int distance, duration, usStart, lastUSread; //ultrasonic sensor variables
volatile bool usSent=false; //is expecting an ultrasonic echo

//driving PID variables
int integral=0;
int lastError=0;

int vMode=V_STOP;
int sMode=S_NONE;

volatile int sGyroLimits=100;

//arc variables
volatile int isArcing=false;
volatile int arcT0=-1;
volatile int arcSpeed=-1;
volatile int gyroLatencyMillis=7;
volatile bool arcCancel=false;

//steering PID variables
volatile int integralY=0;
volatile int lastYError=0;

//handbrake values
volatile int handbrakePos0=-1;
volatile int handbrakeP=200;
volatile int handbrakeI=0;
volatile int handbrakeIntegral=0;

//gyro variables
int lastYaw=0;
int yawOffset=0;
int newYaw=0;
int lastAbsYaw=0;
//Error /360°
int gyroError=14;
volatile int absYaw=0;
volatile int targetYaw=0;

volatile int arcDirection=-1; //-1:left, 1:right
#define ARC_RIGHT 1
#define ARC_LEFT -1
//retievable log variable
int log_var=0;
//stored response to i2c command
int i2cResponse=-1;

volatile int turnRatioL=1000;
volatile int turnRatioR=1000;

int steerPercentage=0;

Adafruit_BNO08x_RVC rvc = Adafruit_BNO08x_RVC(); //gyro communication class in RVC mode
// void setDrivingDirection(int dir){
//   if(dir==1){
//     digitalWrite(PWM_BW_PIN, LOW);
//     digitalWrite(PWM_FW_PIN, HIGH);
//   } else{
//     digitalWrite(PWM_BW_PIN, HIGH);
//     digitalWrite(PWM_FW_PIN, LOW);
//   }
  
// }
//Ultrasonic sensor distance calculating (on echo interrupt)
void echo(){
  if(usSent){
    duration = micros()-usStart;
    int newDistance = (duration*172);
    distance=(distance*8+newDistance*2)/10;
    usSent=false;
  }
}
//Ultrasonic sensor start measure
void sendUSPulse(){
	digitalWrite(US_TRIGGER_PIN, LOW);
  delayMicroseconds(2);
  digitalWrite(US_TRIGGER_PIN, HIGH);
	delayMicroseconds(10);
	digitalWrite(US_TRIGGER_PIN, LOW);
  usStart=micros();
  usSent=true;
}

//timer interrupt, run exactly 100 times a second, handles real speed calulation, PID driving motor control and PID steering control
void IRAM_ATTR onTick(){
  // posAvg=(posL+posR)/2;
  speed=(speed*80+(((posR-lastTicks) * 100)*20))/100;
  lastTicks=posR;
  
  switch(sMode){
    case S_NONE:
    {
      int duty=-1;
      if(steerPercentage>0){
        duty=(SERVO_MAX-SERVO_CENT)*abs(steerPercentage)/100+SERVO_CENT;
      } else {
        duty=SERVO_CENT-(SERVO_CENT-SERVO_MIN)*abs(steerPercentage)/100;
      }
      if(duty>SERVO_MAX) {duty=SERVO_MAX;}
      if(duty<SERVO_MIN) {duty=SERVO_MIN;}
      ledcWrite(S_PWM_PIN,duty);
      break;
    }
    case S_GYRO:
    {
      int yError=absYaw-targetYaw;
      integralY+=yError;
      volatile int percent=(kPY*yError+integralY*kIY+(yError-lastYError)*kDY)/10*-1;
      percent=max(-sGyroLimits,int(min(percent,sGyroLimits)));
      percent*=(vMode==V_BACKWARD)?-1:1;
      int duty=SERVO_CENT;
      if(percent>0){
        duty=(SERVO_MAX-SERVO_CENT)*abs(percent)/100+SERVO_CENT;
      } else {
        duty=SERVO_CENT-(SERVO_CENT-SERVO_MIN)*abs(percent)/100;
      }

      lastYError=yError;
      if(duty>SERVO_MAX) {duty=SERVO_MAX;}
      if(duty<SERVO_MIN) {duty=SERVO_MIN;}
      ledcWrite(S_PWM_PIN,duty);
      break;
    }
    case S_ARC:
    {
      if(true){
        int duty=-1;
        if(steerPercentage>0){
          duty=(SERVO_MAX-SERVO_CENT)*abs(steerPercentage)/100+SERVO_CENT;
        } else {
          duty=SERVO_CENT-(SERVO_CENT-SERVO_MIN)*abs(steerPercentage)/100;
        }
        if(duty>SERVO_MAX) {duty=SERVO_MAX;}
        if(duty<SERVO_MIN) {duty=SERVO_MIN;}
        ledcWrite(S_PWM_PIN,duty);
      }


      int predictedYaw=absYaw+arcSpeed*(gyroLatencyMillis/10);
      // int predictedYaw=absYaw;
      // Serial.println("pyawe:");
      // Serial.println(predictedYaw);
      // Serial.println("smode "+sMode+" targetyaw "+targetYaw+" arcdir "+arcDirection+" predictedyaw "+predictedYaw);
      if((((arcDirection==ARC_RIGHT && predictedYaw>=targetYaw) || (arcDirection==ARC_LEFT && predictedYaw<=targetYaw)) && isArcing)){
        isArcing=false;
        steer(0);
        arcT0=millis();
        // setLedStatus(STATUS_CONNECTED);
      }

      if(millis()>=arcT0+gyroLatencyMillis && !isArcing) {
        sMode=S_GYRO;
      }
      if(arcCancel) {
        arcCancel=false;
        isArcing=false;
        sMode=S_GYRO;
      }
      break;
    }
  }
  switch(vMode){
    case V_UNREGULATED:
    {
      if(unregPower>0){
        ledcWrite(PWM_BW_PIN, 0);
        ledcWrite(PWM_FW_PIN, int(4095/100*abs(unregPower)));
      } else{
        ledcWrite(PWM_FW_PIN, 0);
        ledcWrite(PWM_BW_PIN, int(4095/100*abs(unregPower)));
      }
      // ledcWrite(PWM_PIN_R, 1000);
      // ledcWrite(PWM_PIN_L, 1000);
      // ledcWrite(PWM_PIN_R, int(4095/100*abs(unregPower)));
      break;
    }
    case V_STOP:
    {
      // ledcWrite(PWM_PIN_L, 0);
      ledcWrite(PWM_BW_PIN, 0);
      ledcWrite(PWM_BW_PIN, 0);
      break;
    }
    case V_FORWARD:
    {
      // Serial.println("s, l ,r");
      // Serial.println(speed);
      // Serial.println(posL);
      // Serial.println(posR);
      int error=targetSpeed-speed;
      integral+=error;
      int PWM=kP*error+integral*kI+(error-lastError)*kD;
      lastError=error;
      PWM=std::max(-4095/10,PWM);
      PWM=std::min(4095,PWM);
      
      if(PWM<0){
        ledcWrite(PWM_FW_PIN, 0);
        ledcWrite(PWM_BW_PIN, abs(PWM));
      } else{
        ledcWrite(PWM_BW_PIN, 0);
        ledcWrite(PWM_FW_PIN, abs(PWM));
      }
      // ledcWrite(PWM_PIN_L, abs(PWM));
      // ledcWrite(PWM_PIN_R, abs(PWM));
      // ledcWrite(PWM_PIN_L, 1000);
      // ledcWrite(PWM_PIN_R, 1000);
      break;
    }
    case V_BACKWARD:
    {
      int error=targetSpeed-speed;
      integral+=error;
      int PWM=(kP*error+integral*kI+(error-lastError)*kD);
      PWM*=-1;

      lastError=error;
      PWM=std::max(-4095/10,PWM);
      PWM=std::min(4095,PWM);
      if(PWM<0){
        ledcWrite(PWM_BW_PIN, 0);
        ledcWrite(PWM_FW_PIN, abs(PWM));
      } else{
        ledcWrite(PWM_FW_PIN, 0);
        ledcWrite(PWM_BW_PIN, abs(PWM));
      }
      // ledcWrite(PWM_PIN_L, abs(PWM));
      // ledcWrite(PWM_PIN_R, abs(PWM));
      break;
    }
    case V_BRAKE:
    {
      if(abs(speed)<100){
        handbrakePos0=posR;
        handbrakeI=0;
        vMode=V_STOP;
        break;
      }
      int brake=brakePowerPercent*pow(2,motor_pwm_res)/100;
      if(speed<0){
        ledcWrite(PWM_BW_PIN, 0);
        ledcWrite(PWM_FW_PIN, std::min(brake,4095));
      } else {
        ledcWrite(PWM_BW_PIN, std::min(brake,4095));
        ledcWrite(PWM_FW_PIN, 0);

      }
      
      // ledcWrite(PWM_PIN_R, brake);
      break;
    }
    case V_HANDBRAKE:
    {
      ledcWrite(PWM_BW_PIN, 4095);
      ledcWrite(PWM_FW_PIN, 4095);
      // int PWM=0;
      // int error=posR-handbrakePos0;
      // handbrakeIntegral+=error;
      // if(abs(error)>10){
      //   PWM=error*handbrakeP+handbrakeIntegral*handbrakeI;
      //   if(PWM<0){
      //     ledcWrite(PWM_BW_PIN, 0);
      //     ledcWrite(PWM_FW_PIN, std::min(4095,abs(PWM)));
      //   } else {
      //     ledcWrite(PWM_FW_PIN, 0);
      //     ledcWrite(PWM_BW_PIN, std::min(4095,abs(PWM)));
      //   } 
      // } else{
      //   ledcWrite(PWM_BW_PIN, 0);
      //   ledcWrite(PWM_FW_PIN, 0);
      //   PWM=0;
      // }
      // ledcWrite(PWM_PIN_L, std::min(4095,abs(PWM)));
      // ledcWrite(PWM_PIN_R, std::min(4095,abs(PWM)));

      break;
    }
  }
}

void setup() {
  // begin
  Serial.begin(115200);
  Serial.println("START");
  //driving PWM setup
  // ledcAttach(PWM_PIN_L, motor_pwm_freq, motor_pwm_res);
  ledcAttachChannel(PWM_BW_PIN, motor_pwm_freq, motor_pwm_res, 0);
  ledcAttachChannel(PWM_FW_PIN, motor_pwm_freq, motor_pwm_res, 2);
  // ledcAttach(PWM_PIN_R, motor_pwm_freq, motor_pwm_res);

  //lidar PWM speed control setup
  // pinMode(LIDAR_PWM_PIN, OUTPUT);
  // digitalWrite(LIDAR_PWM_PIN, LOW);
  ledcAttachChannel(LIDAR_PWM_PIN, lidar_pwm_freq, lidar_pwm_res, 4);
  // ledcAttach(LIDAR_PWM_PIN, lidar_pwm_freq, lidar_pwm_res);
  Serial.println("succesfull?");
  Serial.println(ledcWrite(LIDAR_PWM_PIN, 2048)); //enable PWM control
  delay(1000);
  ledcWrite(LIDAR_PWM_PIN,3440);
  delay(1000);
  ledcWrite(LIDAR_PWM_PIN, 0);

  // ledcDetach(LIDAR_PWM_PIN);
  // delay(3000);
  // ledcChangeFrequency(LIDAR_PWM_PIN, 30, lidar_pwm_res);
  // ledcWrite(LIDAR_PWM_PIN, 700);
  // pinMode(LIDAR_PWM_PIN, OUTPUT);
  // digitalWrite(LIDAR_PWM_PIN, LOW);
  // ledcWrite(LIDAR_PWM_PIN, 2048);

  //timer interrupts
  hw_timer_t *timer=NULL;
  timer=timerBegin(10000);
  timerAttachInterrupt(timer, &onTick);
  timerAlarm(timer,100,true,0);

  //servo pwm
  ledcAttachChannel(S_PWM_PIN, spwm_freq, spwm_res,6);
  ledcWrite(S_PWM_PIN, SERVO_CENT);

  //encoder
  pinMode(A_PIN_L, INPUT);
  pinMode(B_PIN_L, INPUT);
  pinMode(A_PIN_R, INPUT);
  pinMode(B_PIN_R, INPUT);
  attachInterrupt(digitalPinToInterrupt(A_PIN_L), readEncoder<'B','L'>, RISING);
  attachInterrupt(digitalPinToInterrupt(B_PIN_L), readEncoder<'A','L'>, RISING);
  attachInterrupt(digitalPinToInterrupt(A_PIN_R), readEncoder<'B','R'>, RISING);
  attachInterrupt(digitalPinToInterrupt(B_PIN_R), readEncoder<'A','R'>, RISING);
  //Ultrasonic sensor pins setup
  // pinMode(US_TRIGGER_PIN, OUTPUT);
  // pinMode(US_ECHO_PIN, INPUT);
  // attachInterrupt(digitalPinToInterrupt(US_ECHO_PIN), echo, FALLING); //function 'echo' gets called when measurement is done
  
  //led
  pinMode(LED_PIN,OUTPUT);
  // ledcAttachPin(LED_PIN, LED_C);
  // ledcSetup(LED_C, 4, 8);
  setLedStatus(STATUS_SYNCING);
  
  //Serial communication (raspberry)
  PiSerial.setPins(SRL_RX_PIN,SRL_TX_PIN);
  PiSerial.begin(115200);

  //IMU (gyro)
  Serial2.setPins(IMU_RX_PIN, IMU_TX_PIN);  
  Serial2.begin(115200);
  rvc.begin(&Serial2);

  //I2C COMM (raspberry)
  // Wire.setPins(I2C_SDA_PIN,I2C_SCL_PIN);
  // Wire.begin(I2C_ADDRESS);
  // Wire.onReceive(onI2CReceive);
  // Wire.onRequest(onI2CRequest);
  
}
//C++ template in order to avoid having to write 4 slightly different encoder pin detector methods. Keeps track of motors position.
template<char AorBToCheck,char side>
void readEncoder(){
  int pinToCheck=(AorBToCheck=='A' ? side=='L'? A_PIN_L : A_PIN_R  : side=='L' ? B_PIN_L : B_PIN_R);
  if(digitalRead(pinToCheck)==(AorBToCheck=='B')){
    side=='L' ? posL++ : posR--;
    
  } else {
    side=='L' ? posL-- : posR++;
    
  }
}
void setLedStatus(int status){
  switch(status){
    case STATUS_SYNCING:
      digitalWrite(LED_PIN,LOW);
      break;
    case STATUS_CONNECTED:
      digitalWrite(LED_PIN,HIGH);
      break;
  }
}
//called if sync between ESP and raspberry is broken, immediately stops all motors and resets the servo
void disconnect(){
  Serial.println("in disconnect");
  vMode=V_HANDBRAKE;
  steerPercentage=0;
  sMode=S_NONE;
  conn_state=STATUS_SYNCING;
  // ledcWrite(PWM_PIN_L,0);
  // ledcWrite(PWM_PIN_R,0);
  ledcWrite(PWM_BW_PIN, 0);
  ledcWrite(PWM_FW_PIN, 0);
  setLedStatus(STATUS_SYNCING);
}
//sends an int to the raspberry pi via serial
void sendInt(int data){
  for(int i=0;i<4;i++){
    PiSerial.write((data>>(8*i)) & 255);
  }
}
//reads an incoming int from the raspberry via serial
int readInt(){
  int num=0;
  Serial.println("in readInt");
  for(int i=0;i<3;i++){
    while (PiSerial.available() == 0);
    int b=PiSerial.read();
    num=((num>>8) | (b<<((3-1)*8)));
  }
  if (num>=(std::pow(2,(3*8-1)))){
    num-=std::pow(2,(3*8));
  }
  Serial.println(num);
  return num;
}

void steer(int percentage){
  steerPercentage=percentage;
}
//Send packet containing all data collected by the ESP to the Raspberry Pi via Serial protocol
void sendPacket() {
  int checkSum=1;
  PiSerial.write('E'); //1
  PiSerial.write('S'); //2
  PiSerial.write('P'); //3
  int conn_state_t=conn_state;
  PiSerial.write(conn_state_t); //4
  checkSum+=(conn_state_t%256);
  int absYaw_t=absYaw;
  sendInt(absYaw_t); //8
  checkSum+=(absYaw_t%256);
  int posL_t=posL;
  sendInt(posL_t); //12
  checkSum+=(posL_t%256);
  int posR_t=posR;
  sendInt(posR_t); //16
  checkSum+=(posR_t%256);
  int vMode_t=vMode;
  PiSerial.write(vMode_t); //17
  checkSum+=(vMode_t%256);
  int sMode_t=sMode;
  PiSerial.write(sMode_t); //18
  checkSum+=(sMode_t%256);
  int speed_t=speed;
  sendInt(speed_t); //22
  checkSum+=(speed_t%256);
  int log_var_t=log_var;
  sendInt(log_var_t); //26
  checkSum+=(log_var_t%256);

  checkSum%=256;
  sendInt(checkSum); //30 bytes per packet


  log_var++;
}
//main loop
void loop() {
  int t=millis();
  BNO08x_RVC_Data heading;
  // log_var=t-heartBeatT0;
  //checks if there is new gyro data available, if yes, updates internal absyaw variable. Also prevents the gyro from looping around
  if (rvc.read(&heading)) {
    newYaw=heading.yaw*10; //data is in .1 degrees, 1.4° error/360° (over)
    
    if(newYaw-lastYaw>1800) {yawOffset-=3600;}
    if(newYaw-lastYaw<-1800){yawOffset+=3600;}
    
    absYaw=(int)((newYaw+yawOffset)/(1+(float)gyroError/3600));
    if(abs(absYaw-lastAbsYaw)>2) {
      // Serial.print("gyro error ");
      // Serial.println(gyroError);
      // Serial.print("absyaw ");
      // Serial.println(absYaw);
    }
    arcSpeed=absYaw-lastAbsYaw;
    lastYaw=newYaw;
    lastAbsYaw=absYaw;
    sendPacket();
  } else{
    // Serial.println("no data");
  }
  if (PiSerial.available()){
    int command=PiSerial.read();  
    if (conn_state==STATUS_CONNECTED){
      switch(command){
        case CMD_STEER:
          steer(readInt());
          break;
        case CMD_SET_SERVO_CENT:
          SERVO_CENT=readInt();
          break;
        case CMD_SET_SERVO_MAX:
          SERVO_MAX=readInt();
          break;
        case CMD_SET_SERVO_MIN:
          SERVO_MIN=readInt();
          break;
        case CMD_SET_GYRO_P:
          kPY=readInt();
          break;
        case CMD_SET_GYRO_D:
          kDY=readInt();
          break;
        case CMD_SET_SPCTRL_P:
          kP=readInt();
          break;
        case CMD_SET_SPCTRL_D:
          kD=readInt();
          break;
        case CMD_SET_SPCTRL_I:
          kI=readInt();
          break;
        case CMD_SET_ARCCANCEL:
          arcCancel=(readInt()==1);
          break;
        case CMD_SET_GYROERROR:
          Serial.print("SET GYROEEROR ");
          
          gyroError=readInt();
          Serial.println(gyroError);
          break;
        case CMD_SET_HANDBRAKE_P:
          handbrakeP=readInt();
          break;
        case CMD_SET_ARCDIR:
          arcDirection=readInt();
          break;
        case CMD_SET_GYRO_L_MILLIS:
          gyroLatencyMillis=readInt();
          break;
        case CMD_SET_SGYRO_LIMITS:
          sGyroLimits=readInt();
          break;
        case CMD_HEARTBEAT:
          //resets last heartbeat 
          conn_state=STATUS_CONNECTED;
          setLedStatus(STATUS_CONNECTED);
          heartBeatT0=millis();
          // Serial.println(speed);
          break;
        case CMD_SET_VMODE:
        {
          Serial.println("set vmode");
          int data=readInt();
          //checks if vmode is valid
          if(data==V_FORWARD || data==V_BACKWARD || data==V_BRAKE || data==V_STOP || data==V_UNREGULATED || data==V_HANDBRAKE){
            if(data==V_HANDBRAKE) {
              handbrakePos0=posR;
              handbrakeIntegral=0;
            }
            vMode=data;
            
          }
        }
          break;
        case CMD_SET_TARGETSPEED:
          targetSpeed=readInt();
          break;
        case CMD_SET_SMODE:
        {
          int data=readInt();
          Serial.println("smode");
          if(data==S_ARC) {
            isArcing=true;
            arcCancel=false;
            Serial.println("sarc");
            Serial.println(absYaw);
          }
          if(data==S_NONE || data==S_GYRO || data==S_ARC){
            sMode=data;
          }
        }
          break;
        case CMD_SET_BREAKPERCENT:
          brakePowerPercent=readInt();
          break;
        case CMD_SET_TARGET_YAW:
          targetYaw=readInt();
          Serial.println("tyaw set");
          Serial.println(targetYaw);
          break;
        case CMD_SET_UNREG:
          Serial.println("set unreg");
          unregPower=readInt();
          break;
      }
    } else {
      if (command==CMD_HEARTBEAT){
        //resets last heartbeat 
          conn_state=STATUS_CONNECTED;
          setLedStatus(STATUS_CONNECTED);
          heartBeatT0=millis();
      }
    }
    
  }
  int hb=heartBeatT0;
  //Heartbeat detetction, if the raspberry hasn't sent a hearrtbeat command in .5 seconds it assumes the program on the pi may have crashed or stopped
  if((conn_state==STATUS_CONNECTED) && (t-hb)>500) {
    Serial.println("disconnect!");
    disconnect();
  }
  if(t-lastUSread>US_DELAY){
    // sendUSPulse();
    lastUSread=t;
  }

}

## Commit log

2025-05-23 added up-to-date code
    includes switching to using a rapberry pi camera module instead of the pixy cam
2025-06-23 first (wip) draft of hardware documentation
    some images are outdated, along the entire section of 3D printed parts
    [Camera stand 2 v1.f3d, Camera stand 2 v1.stl, Camera stand 2 v2.f3d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]
2025-06-24 updated images and principles
    [pinouts.xlsx]
2025-06-25 Update README.md
    updating the 3d prints section
2025-06-25 Delete models directory
    deleting directory to wipe its content, going to readd it with the correct files
    [Camera stand 2 v1.f3d, Camera stand 2 v1.stl, Camera stand 2 v2.f3d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]
2025-06-25 Added the contents of the model directory
    [Camera final.f3d, Camera final.stl, Lidar mount.f3d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]
2025-11-05 2025+src docs
    [Camera stand 2 v1.f3d, Camera stand 2 v1.stl, Camera stand 2 v2.f3d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]
2025-11-11 updated documentation
    [pinouts.xlsx]
2025-11-14 Update README with PCB and wheel design details
    Added notes on PCB wiring and modifications to wheel design.
2025-11-14 Adding the files for the new wheels
    [nutted wheel.f3d, nutted wheel.stl, wheel original.stl]
2025-11-15 updated power documentation
